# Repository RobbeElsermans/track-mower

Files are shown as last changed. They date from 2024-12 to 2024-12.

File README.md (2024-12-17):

# Track-Mower
A conceptual grass mower equipped with tracks for enhanced mobility.

## Overview
The Track-Mower is built around the ESP D1 Mini microcontroller, which provides WiFi, Bluetooth, and BLE capabilities. Communication between the driver and the mower is established via Bluetooth. Commands are sent as single characters, with each character corresponding to a specific action the mower will execute for a predefined duration.

## Features
- **Microcontroller**: ESP D1 Mini with WiFi, Bluetooth, and BLE.
- **Command-based Control**: Simple single-character commands for predefined actions.
- **Bluetooth Communication**: Reliable connection between the mower and a smartphone.

## How to Use
To operate the Track-Mower:
1. Install the [Serial Bluetooth Terminal](https://play.google.com/store/apps/details?id=de.kai_morich.serial_bluetooth_terminal) app on your Android device.
2. Pair your smartphone with the Track-Mower via Bluetooth.
3. Use the app to send commands to the mower.

## Command List
The following commands can be used to control the Track-Mower:

| Command | Action | Duration  | Description |
|---|---|---|---|
| **F** | Forward  | 1 second  | Moves the mower forward. |
| **B** | Backward | 1 second  | Moves the mower backward. |
| **R** | Right | 0.5 second| Turns the mower to the right using both tracks. |
| **L** | Left | 0.5 second| Turns the mower to the left using both tracks.  |
| **M** | Mower | Gradual | Spins up the blades gradually. |

### Example Usage
To drive the mower forward for 2 seconds, turn left, and then start the blades:
```
F
F
L
M
```

## What to print
- 1x [Battery_assemblyBattery_holder](track-mower/CAD/3D_printing/tank_mower-Battery_assemblyBattery_holder.stl)
- 1x [chassis_body_V2](track-mower/CAD/3D_printing/tank_mower-chassis_body_V2.stl )
- 2x [Track_assemblybearing002](track-mower/CAD/3D_printing/tank_mower-Track_assemblybearing002.stl )
- 2x [Track_assemblybearing_holder_out001](track-mower/CAD/3D_printing/tank_mower-Track_assemblybearing_holder_out001.stl )
- 4x [Track_assemblybearing_holder_out_608002](track-mower/CAD/3D_printing/tank_mower-Track_assemblybearing_holder_out_608002.stl )
- 6x [Track_assemblyExtender](track-mower/CAD/3D_printing/tank_mower-Track_assemblyExtender.stl )
- 2x [Track_assemblyFollower](track-mower/CAD/3D_printing/tank_mower-Track_assemblyFollower.stl )
- 6x [Track_assemblyOverWheel](track-mower/CAD/3D_printing/tank_mower-Track_assemblyOverWheel.stl )
- 2x [Track_assemblyPuller001](track-mower/CAD/3D_printing/tank_mower-Track_assemblyPuller001.stl )
- 58x [Track_assemblytrack](track-mower/CAD/3D_printing/tank_mower-Track_assemblytrack.stl )
- 2x [Track_assemblyTrack_plate](track-mower/CAD/3D_printing/tank_mower-Track_assemblyTrack_plate.stl )
- 6x [Track_assemblyWasher](track-mower/CAD/3D_printing/tank_mower-Track_assemblyWasher.stl)
- 1x [Track_assemblyWasher](track-mower/CAD/3D_printing/Blade.stl)

## Other things
- 608ZZ bearings
- M3 washers, nuts and bolts
- Hot glue
- PowerPlus adapter
- DC motors
- Controller board

## Future Improvements
Here are some ideas for future enhancements:
1. **Advanced Controller**: Develop a controller for precise real-time control of the Track-Mower.
2. **PCB Redesign**: Improve the PCB design to provide more stable current sensing.
3. **Code Optimization**: Refactor the codebase and port it to an RTOS for better performance and scalability.

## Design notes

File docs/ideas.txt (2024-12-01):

Design an electronic menu for ordering food in hospitals.
	--> The patient gets a custom menu for any history related subject.

Create a low-cost negative pressure system for removing fluid from wounds.
	--> Could be helping the wound healing process

Design a go---kart that can be controlled by a joystick for children paralyzed below the waist.
	--> They should also have some fun!

An alarm for an electrician to wear in case he ever got electrocuted
	--> This allerts first aid

Cheap Smart Wheelchair 
	--> Able to drive with joystick and smartphone
	--> Collects data (black box)

chrismas village lights 
	--> A living city

NO -> SMD reflow met strijkijzer met ESP32 en OLED.  

RGB controller, controllable over zigbee or WiFi and IR-led. Also measuring temp, hum & light and send it over on zigbee or WIFI.
	- MOSFET's for leds
	- Temperature sensor
	- Humidity Sensor
	- IR led receiver
	- RF-radio
	- Current sensor (statistical usage)
	- Power management
	- 3D printed case 
	- Lasercut? 

Create a low-cost negative pressure system for removing fluid from wounds.
	--> Could be helping the wound healing process
	- Air pump
	- Tubes 
	- valve?
	- pressure sensor
	- OLED for settings
	- buttons and/ or leds
	
Radio controlled tank mower (small one with "virtual" cutting knives)
	- H-bridge/ ESC
	- brushed / brushless motor
	- bearings
	- tank housing
	- tank tracks
	- gear reductions?
	- Power management
	- Battery powered
	- Controlling? PS3 controller (is bluetooth)

Walk logger for hiking

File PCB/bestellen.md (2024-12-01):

2x fuse holder https://mou.sr/489tumF
2x https://be.farnell.com/multicomp/mccq-121/fuseholder-pcb-mount-ato/dp/1586596

2x fuse 10A https://www.digikey.be/en/products/detail/littelfuse-inc/089107-5NXWS/5233824
https://be.farnell.com/littelfuse/166-7000-5102/automotive-fuse-10a-80vdc/dp/3515901

2x pot 1M https://www.digikey.be/en/products/detail/bourns-inc/TC33X-2-105E/2566882
https://be.farnell.com/bourns/tc33x-2-503e/trimmer-pot-50k-25-1turn-smd/dp/1689867

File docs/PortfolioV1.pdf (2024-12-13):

# Portfolio I-Prototyping

## Robbe Elsermans - s0220625

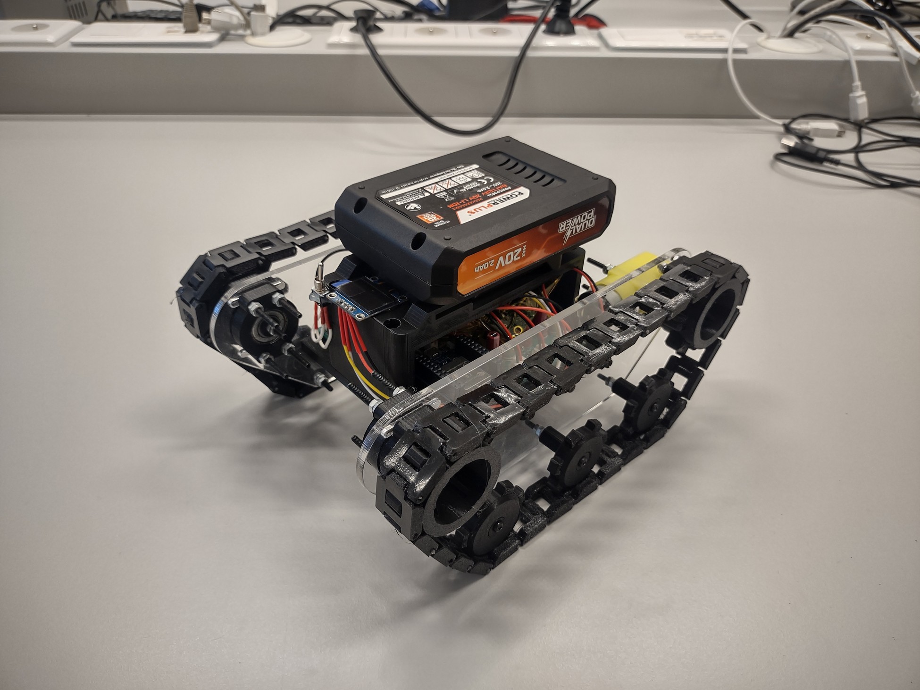
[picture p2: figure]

# Intro

In dit project voor het van I-Prototyping ga ik een rupsvoertuig grasmachine ontwerpen.

Waarom een rupsvoertuig grasmachine?

Een rupsvoertuig is zeer wendbaar in moeilijk bereikbare plaatsen. Echter moet hier soms ook

het gras/ struiken worden afgereden. Huidig doen ze dit met bulldozers waardoor de gehele

grond afgeschraapt wordt. Dit vernietigt het land waarbij bij het afmaaien, de grond intact blijft.

De manual van dit project staat beschreven in de README.md.

# Requirements

Om het project vlot te kunnen starten, heb ik allereerst een opsomming gemaakt wat het

rupsvoertuig grasmachine allemaal nodig kan hebben.

- Actuatoren
o | Motor track links
o | Motor track rechts
o | Motor maai blad
o | Led verlichting
- Sensoren
o | Stroom verbruik
o | Temperatuur
o | Snelheid
o | Locatie
o | Motor Encoder
- Mechanica
o | Rollagers
o | Chassis
o | Trekwielen
o | Volgwielen
o | Rupsband

# 3D model

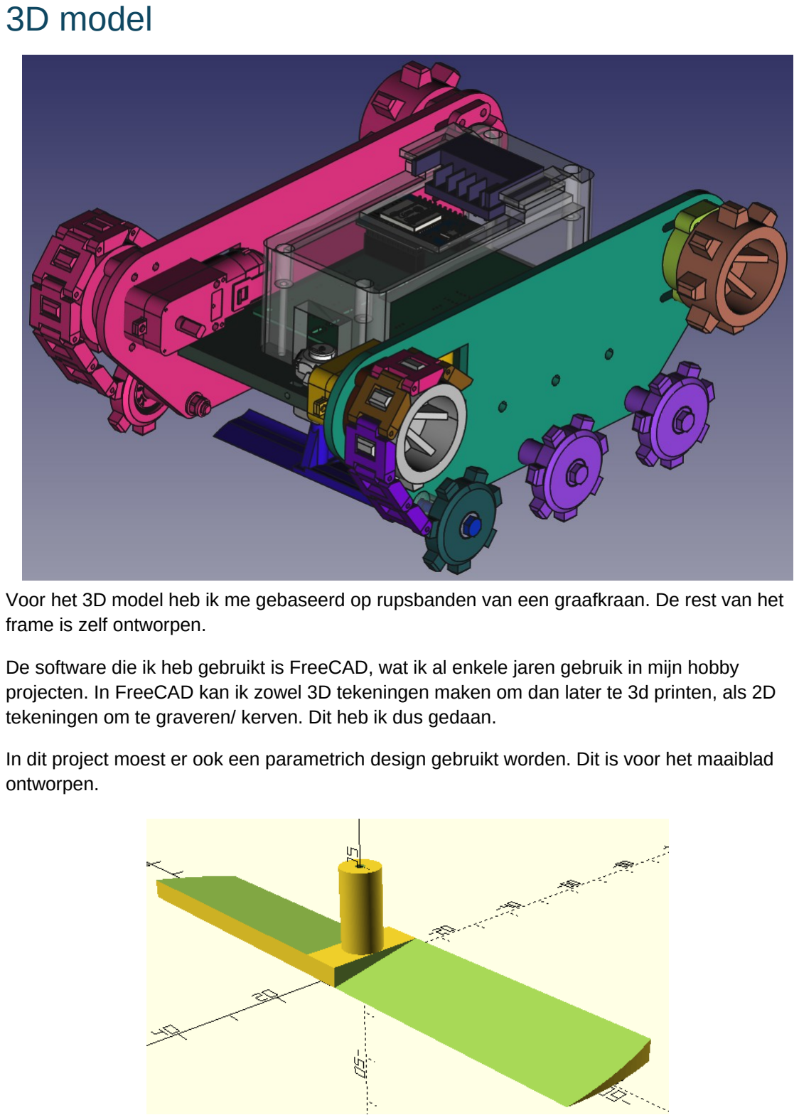
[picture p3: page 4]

Voor het 3D model heb ik me gebaseerd op rupsbanden van een graafkraan. De rest van het

frame is zelf ontworpen.

De software die ik heb gebruikt is FreeCAD, wat ik al enkele jaren gebruik in mijn hobby

projecten. In FreeCAD kan ik zowel 3D tekeningen maken om dan later te 3d printen, als 2D

tekeningen om te graveren/ kerven. Dit heb ik dus gedaan.

In dit project moest er ook een parametrich design gebruikt worden. Dit is voor het maaiblad

ontworpen.

De mechanische componenten zijn zo gekozen dat ze in elke ijzerwinkel te vinden zijn. Behalve

de motoren, deze zijn geselecteerd om op 5V te kunnen opereren en die niet te veel vermogen

vragen. Hierdoor kan ik componenten gebruiken die in het labo ter beschikking gesteld worden.

De rupsketting, zal een aaneenschakeling worden van deeltjes die de gehele rups maken. Om

de rupsketting op spanning te zetten, zal het achterste volgwiel, verschuifbaar zijn om zo de

rups aan te spannen.

De grondwielen zijn in dit design zonder enige vering. Dit zou het project complexer maken

waar jammer genoeg geen tijd voor is.

De plaat waarop de rups tracks geassembleerd word (links en rechts zijn spiegelbeeld), zal uit

Acryl 4mm bestaan die we d.m.v. de laserprinter gaan uitsnijden. Om deze 2 delen te

verbinden, maak ik gebruik van een 3d geprinte chassis. Hierop kan de elektronica en

batterij(en) gemonteerd worden, alsook de motor om het maai-blad aan te sturen.

Het maai-blad zal tussen de tracks staan, waardoor het gras onder het rupsvoertuig mooi kan

worden afgesneden zonder de rupsen of dergelijke te raken.

## 3D Print

De 3D geprinte onderdelen hebben allen een infill van 15%, 2 muren en 5 boven en onder

lagen met een afstand van 0.2mm. Alle onderdelen, behalve de rupsen, zijn in PLA geprint.

Voor de rupsen heb ik voor TPU gekozen omdat deze een elastische eigenschap heeft en ook

wat “plakkeriger” is aan ondergronden door deze elasticiteit. Door de elasticiteit, zal het

rupsvoertuig mobieler zijn op vlakke ondergronden.

De rupsen zijn aan elkaar geschakeld door kleine stukken filament van 1.75mm.

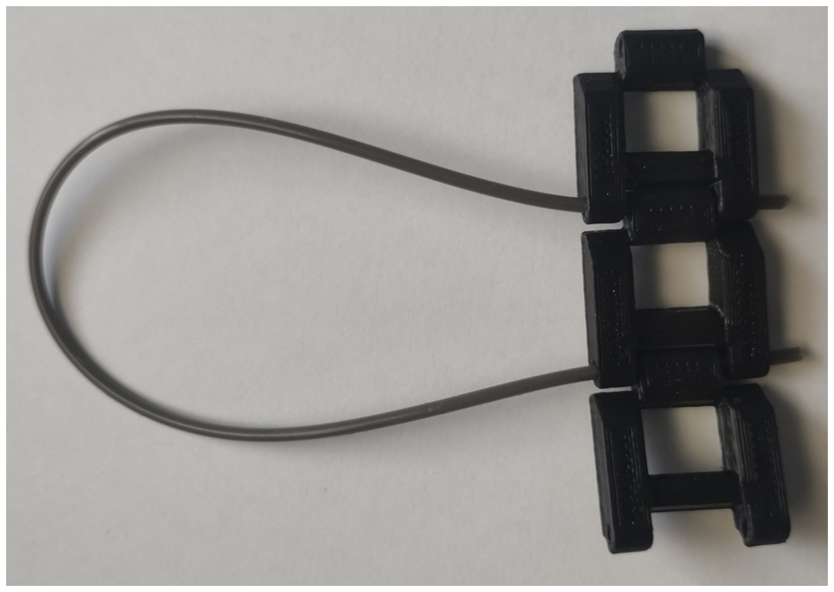
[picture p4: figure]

## Laser Cut

De laser cut machine is gebruikt om de track assemblage op te bevestigen. Deze is met een

snelheid van 15mm/min aan een power van 85% uitgesneden op een Acryl plaat van 4mm dik.

Er werd voor Acryl gekozen omdat deze tegen water kan. Als we gras versnijden, komt er water

vrij. MDF kan hier niet goed tegen.

# Blockschema

Om een globaal overzicht te bekomen, heb ik een blokschema gemaakt. Hierin duid ik aan

welke sensoren en actuatoren ik gebruik en de communicatie tussen deze componenten en de

microcontroller.

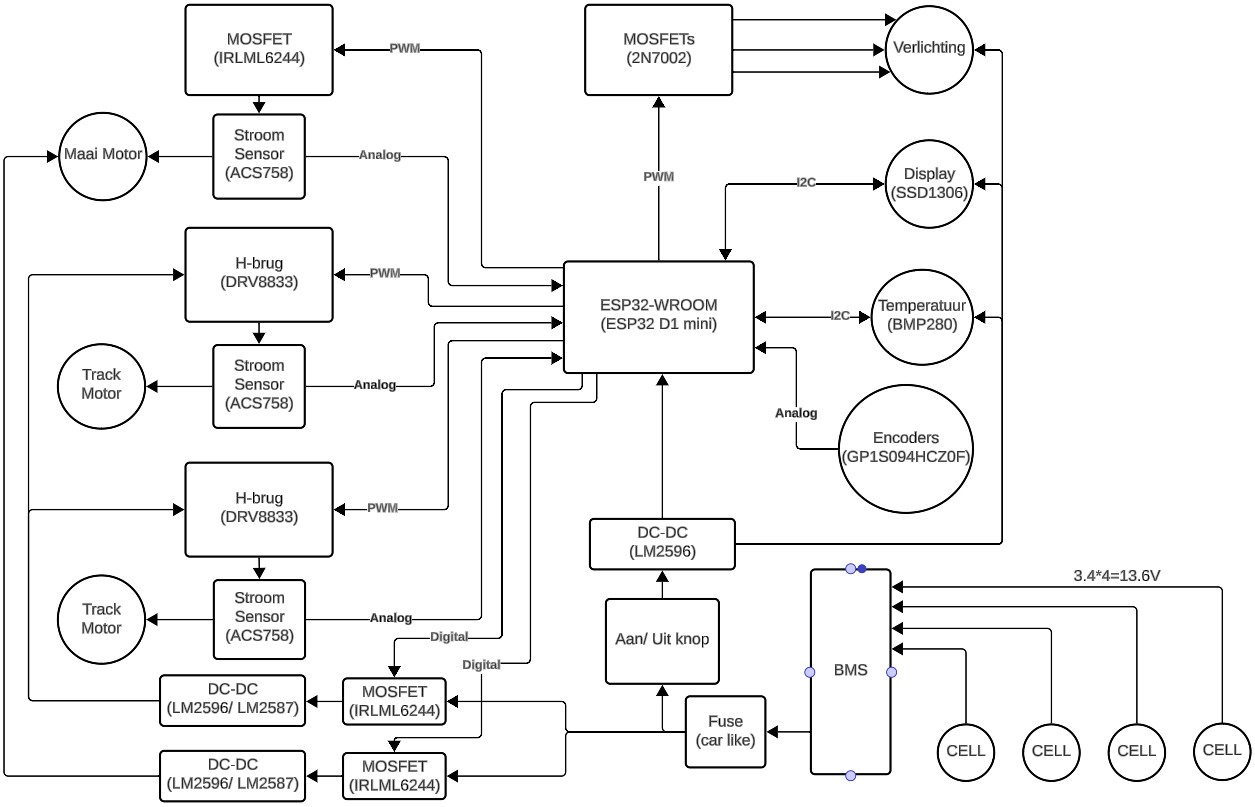
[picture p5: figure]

# Componenten

Referencie | Waarde | Aantal
C1,C4,C6,C7,C10,C24,C26,C28,C31,C32 | 10n | 10

# C2,C16,C17,C18,C19,C20,C21,C22,C23,C25,C27,C33,C34

,C39,C40,C41 | 10µ | 16
C3,C35,C36 | 1µ | 3
C5,C11 | 2.2µ | 2
C8,C14 | 100µ | 2
C9,C15 | 407µ | 2
C37 | 470µ | 1
D5 | D | 1
D6,D7,D8,D9 | LED | 4
D10 | D_Schottky | 1
F1 | MCCQ-121 | 1
J1,J2,J3 | LM2596_modul_in | 3
J4 | BMP280_Module | 1
J5 | BMS_input | 1
J6,J11,J12 | LM2596_modul_out | 3
J7 | On/Off_toggle | 1
J8 | SPI_Connector | 1
J9 | SSD1306 | 1
J10 | I2C_Extender | 1
J13,J14 | GP1S094HCZ0F | 2
M1,M2,M3 | Motor_DC | 3
Q3,Q10,Q12,Q13,Q14,Q15 | 2N7002 | 6
Q4,Q11,Q17 | SI2323 | 3
Q5 | IRLML6244 | 1
Q16,Q18 | Si7141DP | 2
R1,R2,R16,R22,R48,R49,R58,R60,R62 | 10k | 9
R3,R6,R7,R8,R9,R18,R19,R20,R21,R23,R25,R37,R38,R39,
R41,R42,R43,R44,R45,R46,R47,R55,R66 | 1M | 23
R4,R5,R30,R32,R34,R36 | 120 | 6
R10,R11,R12,R13,R14,R15,R40,R63 | 100k | 8
R17,R52,R53 | 3.3k | 3
R24,R50,R51 | 68k | 3
R26 | R | 1
R27,R28 | 4k7 | 2
R29,R31,R33,R35 | 10M | 4
R54 | 2.2M | 1
R56 | 3.3M | 1
R57,R59,R61 | 12k | 3
R64,R65 | 15k | 2

U1,U5,U11 | TLV2775AIN

3
U2,U6,U8 | ACS758xCB-050B-PFF

3
U4,U7 | DRV8833PWP

2
U9 | esp32-wemos-d1-mini

1
U10 | PCF8574

1

# Stroom Verbruik

Component | Maximaal Verbruik (A)
track motor (TT-Motor) | 1.5
track motor (TT-Motor) | 1.5
DC motor 6V | 0.5
Verlichting (LED) | 0.05
Verlichting (LED) | 0.05
Verlichting (LED) | 0.05
Verlichting (LED) | 0.05
Display (SSD1306) | 0.02
Encoder (GP1S094HCZ0F) | 0.05
Encoder (GP1S094HCZ0F ) | 0.05
H-brug (DRV8833) | 0
H-brug (DRV8833) | 0
Totaal | 3.83

De niet vermelde onderdelen hebben zeer kleine stromen die in deze configuratie geen impact

hebben.

# Berekeningen

## Battery voltage scaler

Om de batterij spanning te meten, moeten we gebruik maken van een spanningsdeler. We gebruiken namelijk een 5C Li-Ion (5 cell) batterij in serie geschakeld waardoor we een maximaal voltage krijgen van Vbat=5×4.2V=21V.

De ESP32 heeft een maximaal bereik tot Vcc=3.3V .

Om een zekere veiligheid marge te bekomen, gaan we er vanuit dat de maximale
batterijspanning Vbat=5×4.25V=21.25V is.

Er is dus een spanningsdeler nodig met factor

### Vin

### Vout

=

### V bat

### V cc

=

21.25V
3.3V

=6.43939 ...

De spanningsdeler formule is als volgt: Vout=Vin

R2
R2⁺R1

Stel, we nemen R2=1 M Ω, dan is R1=

VR2

### Vout

# − R2=6.43939∗1 M Ω−1M Ω=5.439 M

Nu voor de E-12 reeks, nemen we 3.3MΩ en 2.2MΩ om uit te komen op 5.5MΩ.

Deze verhoging in waarde, zal de spanning verlagen op de uitgang met een factor.
R2
R1⁺R2

=

1M Ω

# 5.5 MΩ+1MΩ

=0.15384

In code wordt de gemeten spanning dus vermenigvuldigt met | 1
0.153846154

=6.4999999=6.5

## Current sensor low-pass filter

De stroom sensor (met behulp van HALL-effect of elektromagnetisch veld) zal op een PWM gestuurde actuator aangesloten worden. De ingestuurde PWM wordt dus eveneens ingelezen door de sensor. Om de sensor uit te lezen, gaan we dus een analoge filter maken die ons signaal frequentie bereik beperkt van 0Hz tot 50Hz.

Hiermee merken we nog steeds verschillen op die tot en met 1
50Hz

=2ms veranderen.

We bepalen de nodige weerstand in de RC-filter.

f
c=

1

# 2 πRC

R=

1

### 2πf cC

met f

# c=50 Hzen C=1µF wordt dit R=

1

# 2 π50 Hz 1µF

=3183Ω

Of in E-12 reeks 3.3 k Ω. Wat een cut-off frequentie heeft van f
c=

1

# 2 π 3.3 kΩ1µF

=48.22Hz.

## Current sensor readout

De stroom sensor geeft een spanning die lineair verloopt met de gemeten stroom.

Bij 0A, is er een spanning van Viout=

### Vcc

2

waarbij Vcc=3.3V dus viout=1.65V .

Per ampère gemeten, komt hier 40mV bij. Dus algemeen 1.65V ± 40mV / A. Deze kan dus

zowel positief als negatieve stroom (inverse stroomzin) meten.

Doordat de ESP32, met zijn 12-bit ADC, een resolutie heeft van Δ=

3.3V

# 4096 bit =805. 664 µV

zou deze maar een stroom van Δ I=(
40 mV
A

805.664µV )

−1
=0.021416 A

per verschil in bit kunnen

meten. Dit is een te kleine resolutie.

We gaan dus de resolutie terugschroeven naar [−4 A , 4 A] wat het volgende geeft:

# Viout min=1.65V −4 A∗0.0 4

V
A

=1.49V

# Viout max=1.65V +4 A∗0.0 4

V
A

=1.81V

# V Δ=1.81V −1.49V =0.32V

Met een differentieel versterker, kunnen we de verschilspanning V Δ opmeten. We nemen een

versterking van 1. Nadien plaatsen we een niet-inverterende versterker met factor 10.

Deze brengt de spanning van maximaal 0.32V naar 3.2V.

Nu hebben we een een stroom van Δ I=(

400 mV
A

805.664µV )

−1
=0.0 021416 A

per verschil in bit dat

we kunnen meten.

Voor de differentieel versterker, nemen we vier dezelfde weerstanden van 100kΩ. Voor de

referentie spanning van 0 A of 1.49V, gebruiken we een spanning deler met hoge impedantie

ingang (een spanningsvolger). Deze zal met de weerstanden R1tot=1.215 M Ω en R2=1 M Ω.

Of beter een regelbare weerstand van 10kΩ gezet worden.

Voor de niet-inverterende versterker gebruiken we volgende formule om Rf te bepalen:

# Vout=V❑(1+

Rf

# R ) Met Vout=3.2V , V ❑=0.32V , R=10 k Ω geeft

Rf=(

### V out

V ❑

# −1)∗ R=9∗10 k Ω=90 k Ω

# Of in E-12 reeks 68kΩ+12kΩ+10kΩ

## Encoder comparator

De encoder zal een spanning geven in functie van de hoeveelheid licht op de LDR. Om het de MCU wat makkelijker te maken, gaan we dit signaal omzetten naar 2 waardes met een comparator. Dit om op de MCU een trigger te kunnen genereren wanneer er zo’n lichtbrug een object of geen object tussenin heeft.

De comparator zal bij een bepaald voltage, volledig Vcc of GND als uitgang geven.
De waardes die we gaan gebruiken zijn $V_low = 0.5V$ $V_high = 2.4V$. Dit omdat $V_BE =0.4V$.

V ❑=

# (V OH −Vref ) ∗R1

R1⁺R2

### +Vref

Waarbij we R_1 berekenen in excel. Wat het volgende geeft:

V_ref | v_TH | V_TL | R_1 | R_2 | R | V_N | V_P
1.65 | 0.825 | 2.475 | 10000 | 20000 | 2 | 0 | 3.3

Wat in simulatie het volgende geeft:

Met schaal 0.5V/div
Groen is out van opamp
Rood is in van opamp.

Dit is dus correct.

# PCB

Een 2-layer PCB waarbij tal van extra uitbreidingen en alternatieven zijn aangebracht.

Zo hebben we voor elke motor een stroom sensor. Met deze stroom sensor kunnen we bepalen

of dat een motor vast zit of niet. Om alias frequenties te vermijden, is een low-pass filter

toegevoegd. Ook het bereik van de stroom sensor is veel te groot voor de applicatie die weg

gaan gebruiken. Daarom gaan we een differentieel versterker nemen binnen een bepaald

bereik om de nauwkeurigheid te verbeteren binnen ons werkgebied. Zie berekeningen.

Er is een mogelijkheid om de motoren hun spanning omvormer af te zetten. Dit voor

bijvoorbeeld veiligheids-redenen. Er zou ook gewerkt kunnen worden met de LM2596 zijn

aan/uit pin (pin 5) om de spanning omvormer uit te schakelen. Echter is er gebruikt gemaakt

van opbouw modules waarbij deze pin niet naar buiten is gebracht.

De gebruikte motor sturing component (DRV8833) is een chip dat 2 H-bruggen bezit. De

DRV8833 kan een maximaal stroom verwerken van 1.5A (PWP package) per brug. Deze

bruggen kunnen we in parallel aaneen schakelen om dan dubbel zo veel vermogen uit te

brengen. Dus 3A per chip.

De gebruikte motoren geven bij een hoge belasting, 1.5A. We kunnen dus 1 chip per motor

gebruiken (de 2 h-bruggen parallel).

Voor de maai motor, is er gebruikt gemaakt van een N-MOSFET die maar in 1 richting kan

geleiden. De maai motor moet ook maar in 1 richting draaien.

De track motoren zijn brushed motoren die we niet d.m.v. de aansturing kunnen opvolgen i.v.m.

De snelheid. Dit zal dus met een extra component gebeuren genaamd een encoder. Voor de

encoder, maken we gebruik van een lichtbrug en een extra encorder-ring op de motor

geassembleerd. De gebruikte lichtbrug (GP1S094HCZ0F) is een analoog signaal dat lineair

verloopt met de lichtintensiteit. Om dit makkelijk te interpreteren in de MCU, gaan we een

comparator gebruiken om het analoog signaal, als een digitaal signaal aan te leggen bij een

bepaalde treshold (zie berekeningen).

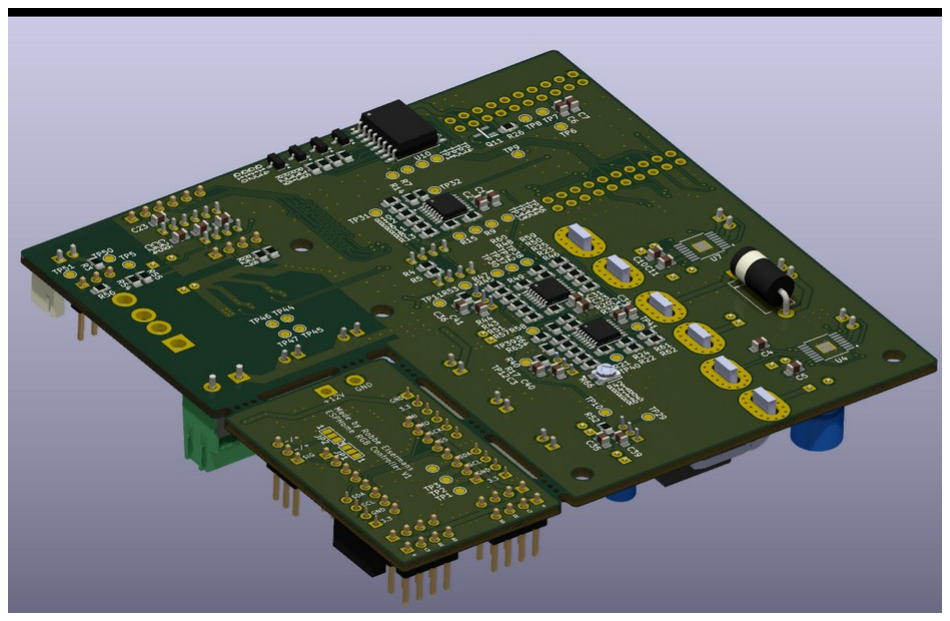
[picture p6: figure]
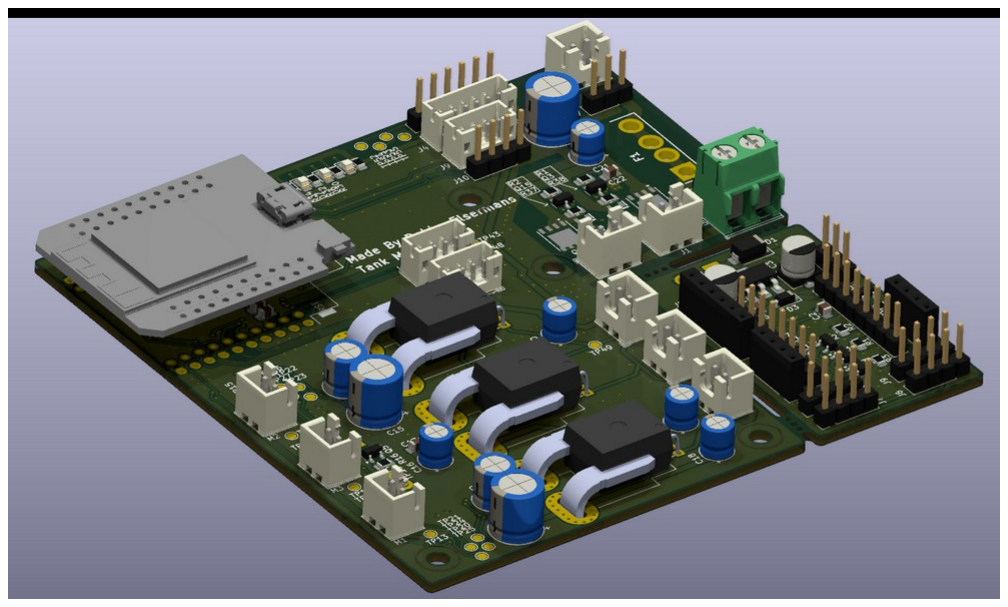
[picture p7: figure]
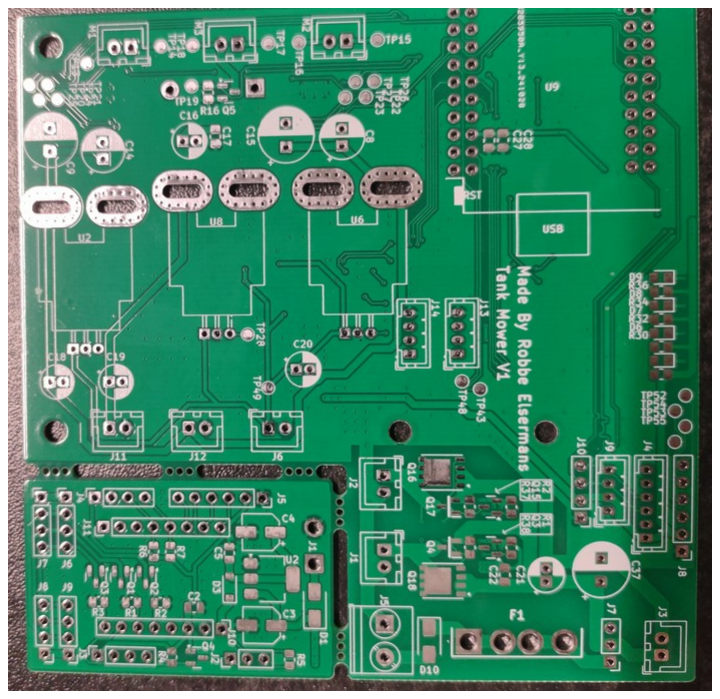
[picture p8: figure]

# Assemblage en testing

Bij het source van de nodige componenten heb ik opgemerkt dat ik een verkeerde package heb

genomen voor de quad-opamp module (TLV2775) namelijk TSSOP. Echter heeft deze een

package van SOP wat dus een verschil geeft. Jammer genoeg was de pcb al in productie

gezet. Dus er was nood aan een nieuwe component met dezelfde footprint en package.

Na wat zoeken is er het volgende gevonden: TLV4333IPWR. Er is een groot verschil in GBP,

maar de toepassing waarin ik deze opamps gebruik mag de GBP laag zijn. Het zijn tenslotten

laag frequente signalen.

Bij het solderen ben ik gestart met al de SMD componenten te solderen beginnende bij de

laagste packages. Voor het solderen, werd er gebruik gemaakt van een SMD reflow plate die

zelf is ontworpen.

Om de PCB grondig te testen, zal ik deze deel per deel opbouwen om zo de werking ervan te

testen.

## I2C bus

Nadien de ESP32, IO-expansie module alsook de 4 leds om te valideren dat de IO-expansie

module correct kan gebruikt worden. Ook de OLED module werd aangesloten.

Om de test visueel te valideren, wordt er 1010 op de OLEd getoond en ook de leds kleuren in

een 1010 patroon.

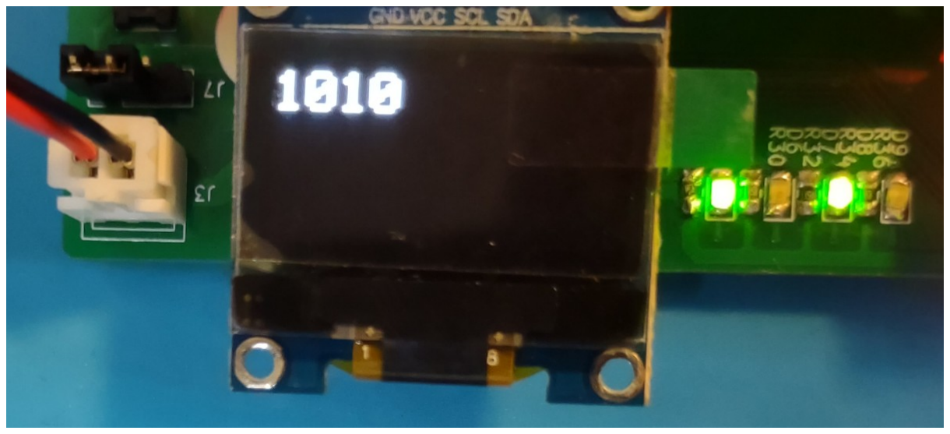
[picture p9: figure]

## VCC switch

Daarna werd de motor P-MOSFETS bevestigd. Na het correct afstellen van de buck-converters

hun uitgangsspanningen, zijn deze door verbonden met de PCB.

Bij het testen van de schakelaars, was er één pin die niet aan of uit wou gaan. Na verder

onderzoek blijkt deze pin (35) een input only pin te zijn. Echter gebruik ik deze als output. Om

dit op te lossen, zal de andere pin (13) gebruikt worden om beide te schakelen. Dit kon

makkelijk opgelost worden door een connectie te maken tussen de testpunten TP43 en TP48.

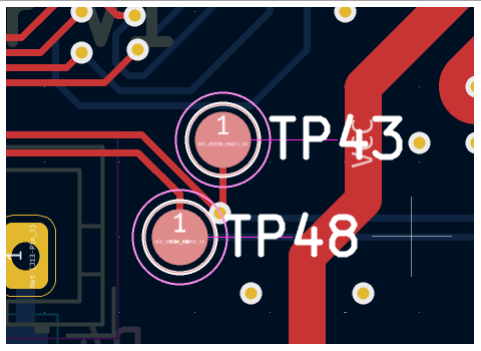
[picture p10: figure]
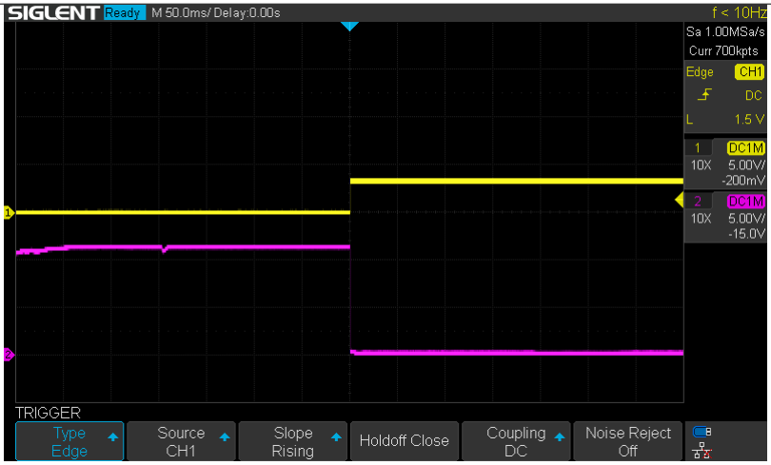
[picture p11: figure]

Scoope beeld waarbij te zien is dat pin 13 hoog komt (GEEL), en daardoor zal ook Q15 en

Q17 schakelen als ook Q16 en Q18 waardoor de Buck-modules gevoed worden met de input

spanning. Aan de gates (PAARS) van de P-MOSFET zal de pull-up spanning dus dalen naar

0V en zo zal de P-MOSFET in geleiding treden.

## H-Brug

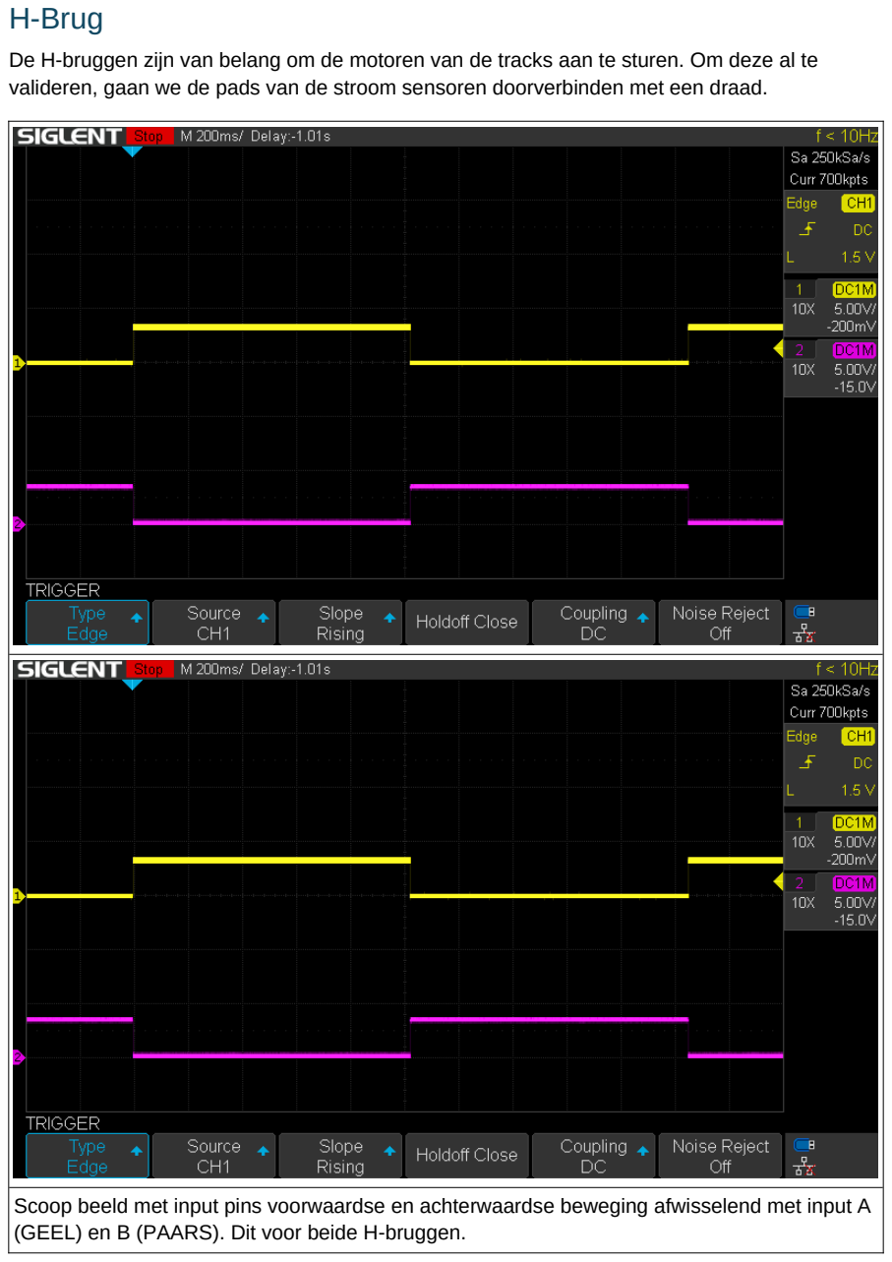
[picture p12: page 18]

De H-bruggen zijn van belang om de motoren van de tracks aan te sturen. Om deze al te

valideren, gaan we de pads van de stroom sensoren doorverbinden met een draad.

Scoop beeld met input pins voorwaardse en achterwaardse beweging afwisselend met input A

(GEEL) en B (PAARS). Dit voor beide H-bruggen.

## Current sensor

Vervolgens werden de stroom sensoren bevestigd. De stroom sensoren zijn van belang om te

bepalen wanneer een motor niet meer kan bewegen door een obstakel of dergelijke. Daarom

zijn er stroom sensoren voorzien die elke motor hun stroom kan meten met een nauwkeurigheid van 2mA en een bereik van [−4 A, 4 A].

FOTO

testopstelling 330Ω weerstand als verbruiker wat 0.05050A neemt bij 5V op de mower motor

connector. Deze is geselecteerd om het makkelijk te kunnen schakelen door de N-MOSFET.

I=

10V
330Ω

=0.05050 A

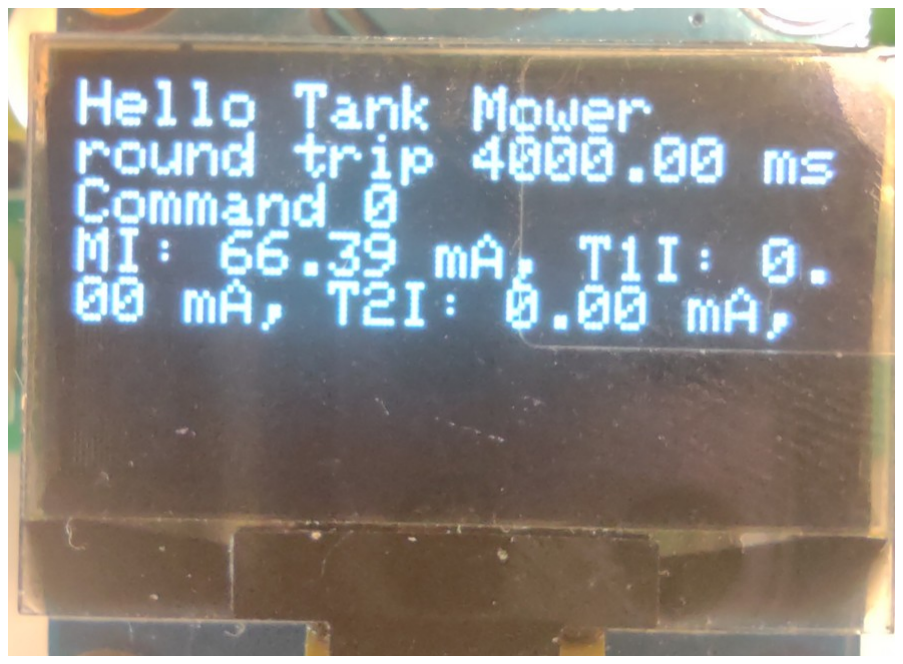
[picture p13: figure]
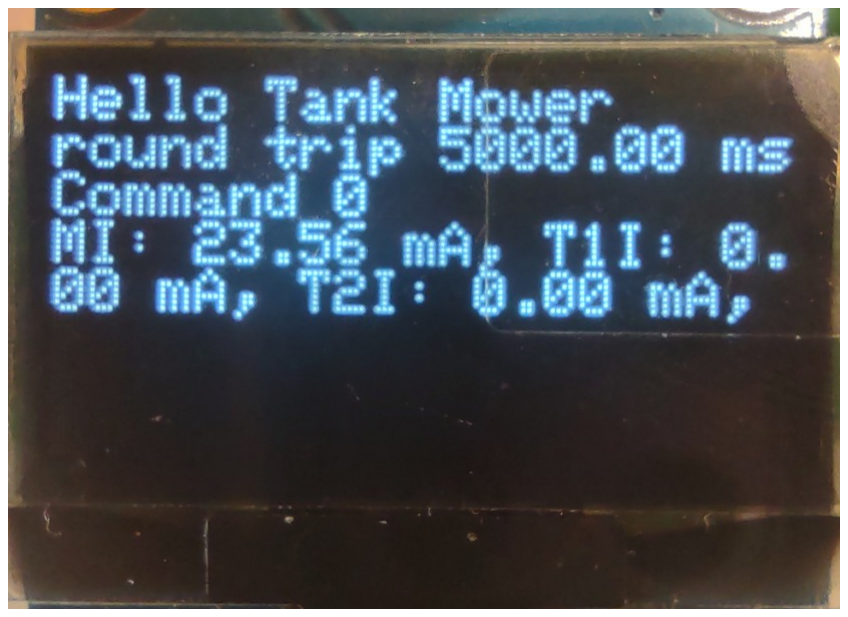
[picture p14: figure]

Op de metingen is duidelijk te zien dat er vrij veel fluctuaties op zitten. Dit komt

hoogswaarschijnlijk door de weerstand tolleranties die een orde groote hebben van 10%. Dit

kan dus de differentiaal versterker en de niet-inverterende versterker van factor 10 beinvloeden

## LP-filter

Om de werking van de LP-filter te valideren, werd er een sinus injectie uitgevoerd op de uitgang

van de stroom sensor die de stroom meet op de mower-motor. De gebruikte sinus is 25Hz,

250Hz en 2.5kHz.

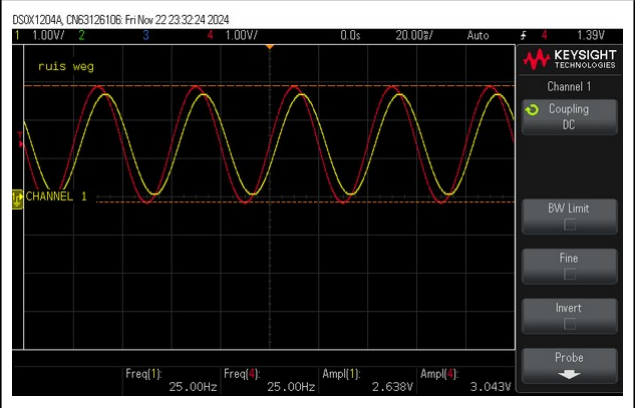
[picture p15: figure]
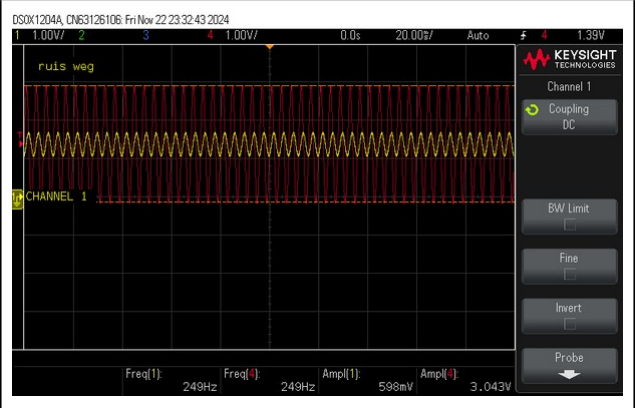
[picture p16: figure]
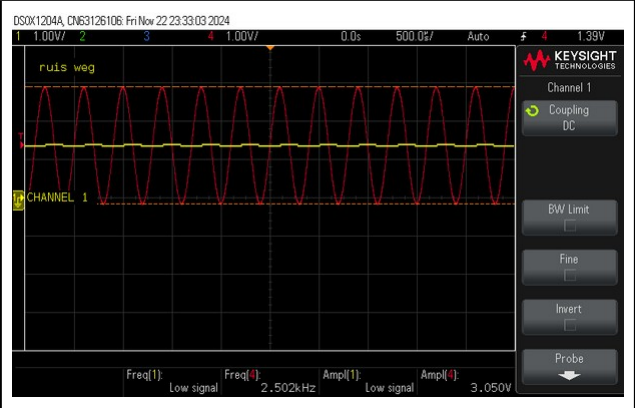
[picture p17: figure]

Scoop beeld met de sinus functie injectie (ROOD) en de response van de LP-filter (GEEL).

25Hz, 250Hz en 2k5Hz respectievelijk.

Er is een mooie attenuatie te zien.

## Batterij spanning

De batterij spanning wordt d.m.v. een spanningsdeler ingelezen in de ESP. Hier maken we

gebruik van een factor 6.5 om de effectieve spanning te weten. We leggen een spanning aan

van 12V wat zou moeten uitkomen op 1.847V.

Echter is hier een probleem met de gekozen pin 12. Wanneer pin 12 niet floating is bij boot, zal

de boot falen. Dit mond uit dat de ESP niet kan opstarten als er een batterij is aangesloten.

Om dit toch te kunnen gebruiken, zijn de functies van pin 12 en pin 35 omgedraait. Hierdoor zijn

beide functies beschikbaar.

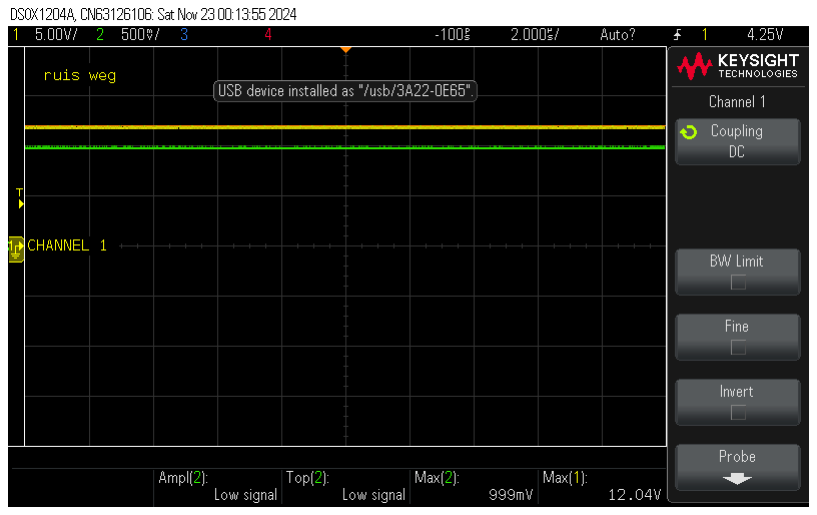
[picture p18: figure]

Een scoop beeld waarbij de ingangsspanning (GEEL) is vergeleken met de uitgangsspanning

na de spanningsdeler (GROEN).

De vooropgestelde waarde van 1.847V blijkt niet te kloppen. Daarom gaan we in de code de

vermenigvuldiger factor wijzigen van 6.5 naar 12.

# Software

Om de complexiteit niet te verhogen, heb ik geen gebruik gemaakt van FreeRTOS om de tank

aan te sturen. De code bevat een finite-state machine waarbij alles zonder enige blocking calls

verloopt (een continue loop).

Hieronder een klein blok diagram die high level uitbeeld wat de code doet.

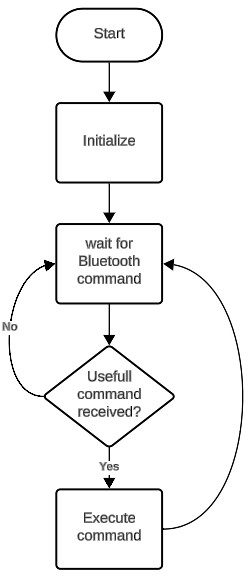
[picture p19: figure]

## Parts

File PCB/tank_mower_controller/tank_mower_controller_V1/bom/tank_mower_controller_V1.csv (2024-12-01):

Reference | Value | Datasheet | Footprint | Qty | DNP
C1,C4,C6,C7,C10,C24,C26,C28,C31,C32 | 10n | ~ | Capacitor_SMD:C_0805_2012Metric_Pad1.18x1.45mm_HandSolder | 10
C2,C16,C17,C18,C19,C20,C21,C22,C23,C25,C27,C33,C34,C39,C40,C41 | 10µ | ~ | -- mixed values -- | 16
C3,C35,C36 | 1µ | ~ | -- mixed values -- | 3
C5,C11 | 2.2µ | ~ | Capacitor_SMD:C_0805_2012Metric_Pad1.18x1.45mm_HandSolder | 2
C8,C14 | 100µ | ~ | Capacitor_THT:CP_Radial_D6.3mm_P2.50mm | 2
C9,C15 | 407µ | ~ | Capacitor_THT:CP_Radial_D8.0mm_P3.50mm | 2
C37 | 470µ | ~ | Capacitor_THT:CP_Radial_D8.0mm_P3.50mm | 1
D5 | D | ~ | Diode_THT:D_DO-201_P12.70mm_Horizontal | 1
D6,D7,D8,D9 | LED | ~ | LED_SMD:LED_0805_2012Metric_Pad1.15x1.40mm_HandSolder | 4
D10 | D_Schottky | ~ | Diode_SMD:D_SMA | 1
F1 | MCCQ-121 |  | mccq-121:MCCQ121 | 1
J1,J2,J3 | LM2596_modul_in | ~ | Connector_JST:JST_XH_B2B-XH-A_1x02_P2.50mm_Vertical | 3
J4 | BMP280_Module | ~ | Connector_JST:JST_PH_B6B-PH-K_1x06_P2.00mm_Vertical | 1
J5 | BMS_input | ~ | TerminalBlock_Phoenix:TerminalBlock_Phoenix_PT-1,5-2-5.0-H_1x02_P5.00mm_Horizontal | 1
J6,J11,J12 | LM2596_modul_out | ~ | Connector_JST:JST_XH_B2B-XH-A_1x02_P2.50mm_Vertical | 3
J7 | On/Off_toggle | ~ | Connector_PinHeader_2.54mm:PinHeader_1x03_P2.54mm_Vertical | 1
J8 | SPI_Connector | ~ | Connector_PinHeader_2.54mm:PinHeader_1x06_P2.54mm_Vertical | 1
J9 | SSD1306 | ~ | Connector_JST:JST_PH_B4B-PH-K_1x04_P2.00mm_Vertical | 1
J10 | I2C_Extender | ~ | Connector_PinHeader_2.54mm:PinHeader_1x04_P2.54mm_Vertical | 1
J13,J14 | GP1S094HCZ0F | ~ | Connector_JST:JST_PH_B4B-PH-K_1x04_P2.00mm_Vertical | 2
M1,M2,M3 | Motor_DC | ~ | Connector_JST:JST_XH_B2B-XH-A_1x02_P2.50mm_Vertical | 3
Q3,Q10,Q12,Q13,Q14,Q15 | 2N7002 | https://www.onsemi.com/pub/Collateral/NDS7002A-D.PDF | Package_TO_SOT_SMD:SOT-23 | 6
Q4,Q11,Q17 | SI2323 | ~ | SI-2323:SOT95P237X112-3N | 3
Q5 | IRLML6244 | https://www.infineon.com/dgdl/Infineon-IRLML6244-DataSheet-v01_01-EN.pdf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 | Package_TO_SOT_SMD:SOT-23 | 1
Q16,Q18 | Si7141DP | https://www.vishay.com/docs/65596/si7141dp.pdf | Package_SO:PowerPAK_SO-8_Single | 2
R1,R2,R16,R22,R48,R49,R58,R60,R62 | 10k | ~ | Resistor_SMD:R_0805_2012Metric_Pad1.20x1.40mm_HandSolder | 9
R3,R6,R7,R8,R9,R18,R19,R20,R21,R23,R25,R37,R38,R39,R41,R42,R43,R44,R45,R46,R47,R55,R66 | 1M | -- mixed values -- | -- mixed values -- | 23
R4,R5,R30,R32,R34,R36 | 120 | ~ | Resistor_SMD:R_0805_2012Metric_Pad1.20x1.40mm_HandSolder | 6
R10,R11,R12,R13,R14,R15,R40,R63 | 100k | ~ | Resistor_SMD:R_0805_2012Metric_Pad1.20x1.40mm_HandSolder | 8
R17,R52,R53 | 3.3k | ~ | Resistor_SMD:R_0805_2012Metric_Pad1.20x1.40mm_HandSolder | 3
R24,R50,R51 | 68k | ~ | Resistor_SMD:R_0805_2012Metric_Pad1.20x1.40mm_HandSolder | 3
R26 | R | ~ | Resistor_SMD:R_0805_2012Metric_Pad1.20x1.40mm_HandSolder | 1
R27,R28 | 4k7 | ~ | Resistor_SMD:R_0805_2012Metric_Pad1.20x1.40mm_HandSolder | 2
R29,R31,R33,R35 | 10M | ~ | Resistor_SMD:R_0805_2012Metric_Pad1.20x1.40mm_HandSolder | 4
R54 | 2.2M | ~ | Resistor_SMD:R_0805_2012Metric_Pad1.20x1.40mm_HandSolder | 1
R56 | 3.3M | ~ | Resistor_SMD:R_0805_2012Metric_Pad1.20x1.40mm_HandSolder | 1
R57,R59,R61 | 12k | ~ | Resistor_SMD:R_0805_2012Metric_Pad1.20x1.40mm_HandSolder | 3
R64,R65 | 15k | ~ | Resistor_SMD:R_0805_2012Metric_Pad1.20x1.40mm_HandSolder | 2
TP1,TP2,TP3,TP4,TP5,TP6,TP7,TP8,TP9,TP10,TP11,TP12,TP13,TP14,TP15,TP16,TP17,TP18,TP19,TP20,TP21,TP22,TP23,TP24,TP25,TP26,TP27,TP28,TP29,TP30,TP31,TP32,TP33,TP34,TP35,TP36,TP37,TP38,TP39,TP40,TP41,TP42,TP43,TP44,TP45,TP46,TP47,TP48,TP49,TP50,TP51,TP52,TP53,TP54,TP55 | TestPoint | ~ | TestPoint:TestPoint_Pad_D1.5mm | 55
U1,U5,U11 | TLV2775AIN | TLV2775AIN | Package_SO:TSSOP-16_4.4x5mm_P0.65mm | 3
U2,U6,U8 | ACS758xCB-050B-PFF | http://www.allegromicro.com/~/media/Files/Datasheets/ACS758-Datasheet.ashx?la=en | Sensor_Current:Allegro_CB_PFF | 3
U4,U7 | DRV8833PWP | http://www.ti.com/lit/ds/symlink/drv8833.pdf | Package_SO:HTSSOP-16-1EP_4.4x5mm_P0.65mm_EP3.4x5mm_Mask2.46x2.31mm_ThermalVias | 2
U9 | esp32-wemos-d1-mini |  | ESP32 D1 Mini:esp32-wemos-d1-mini | 1
U10 | PCF8574 | http://www.nxp.com/docs/en/data-sheet/PCF8574_PCF8574A.pdf | Package_SO:SOIC-16W_7.5x10.3mm_P1.27mm | 1

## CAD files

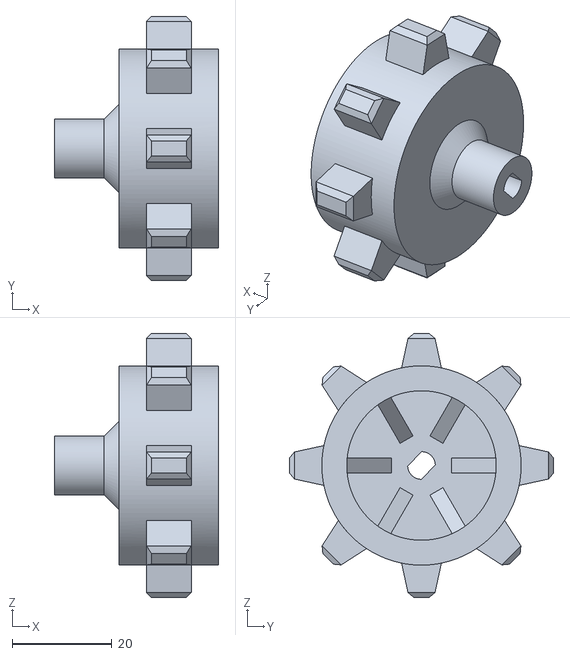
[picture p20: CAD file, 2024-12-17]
CAD/3D_printing/tank_mower-Track_assemblyPuller001.stl
33.0 x 53.0 x 53.0

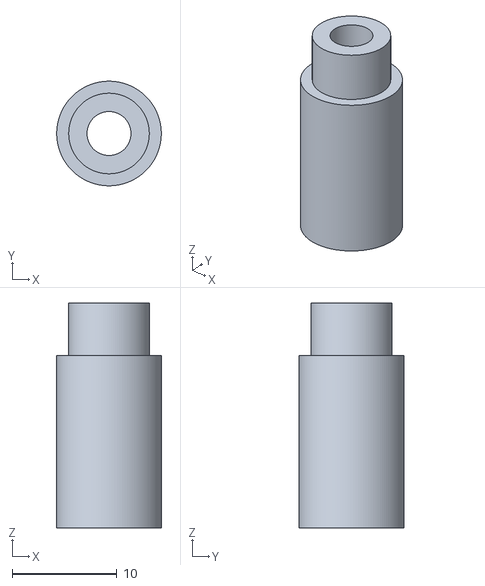
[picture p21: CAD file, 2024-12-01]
CAD/To_3D_print/tank_mower-Track_assemblyExtender.stl
10.00 x 10.0 x 21.5

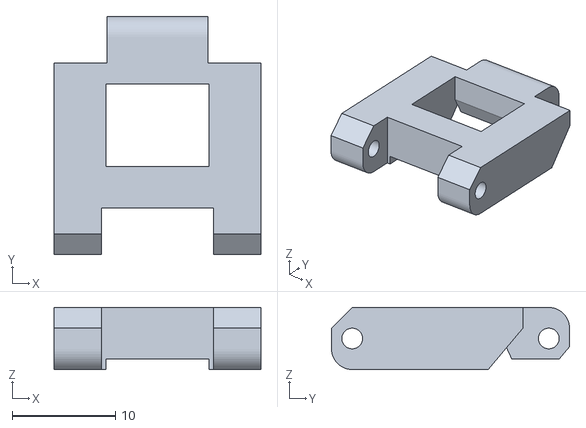
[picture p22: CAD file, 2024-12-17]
CAD/3D_printing/tank_mower-Track_assemblytrack.stl
20.0 x 23.0 x 6.00

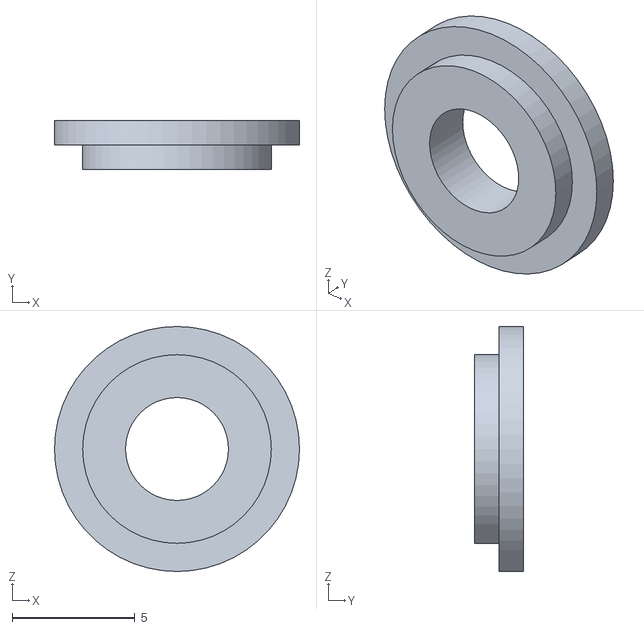
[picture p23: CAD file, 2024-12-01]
CAD/tank_mower-Track_assemblyPocket008.stl
10.0 x 2.00 x 10.0

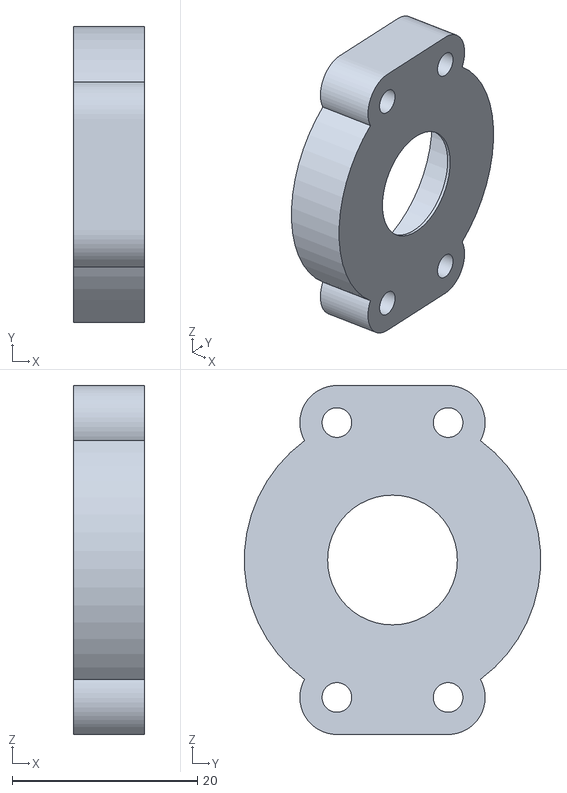
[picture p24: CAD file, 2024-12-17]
CAD/3D_printing/tank_mower-Track_assemblybearing_holder_out001.stl
7.70 x 31.9 x 37.7

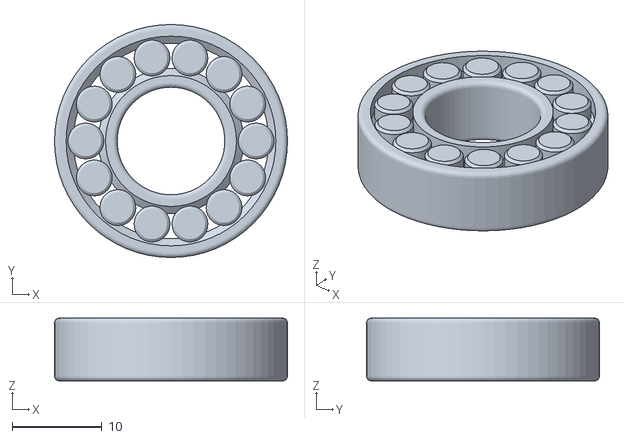
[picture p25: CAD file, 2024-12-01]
CAD/To_3D_print/tank_mower-Track_assemblybearing002.stl
26.0 x 26.0 x 7.00

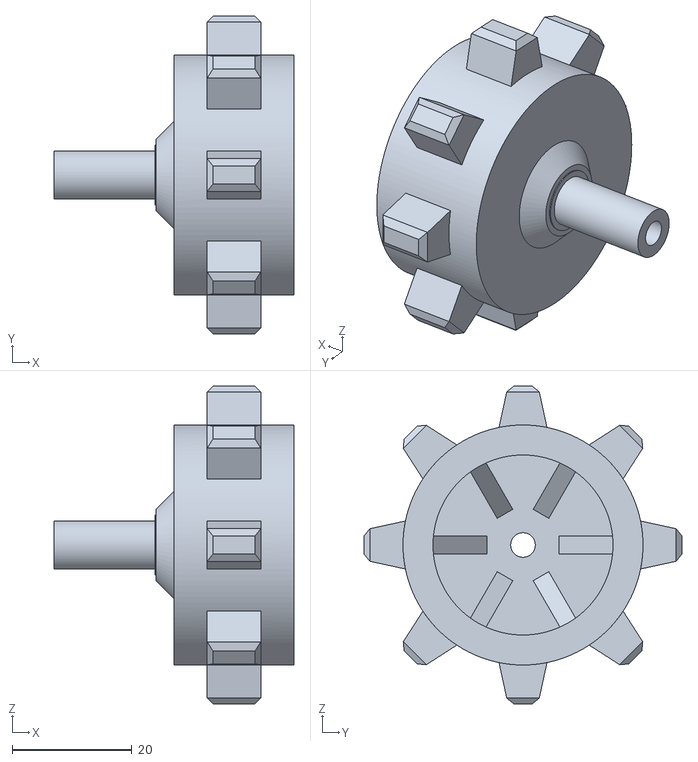
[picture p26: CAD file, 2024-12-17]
CAD/3D_printing/tank_mower-Track_assemblyFollower.stl
40.0 x 53.0 x 53.0

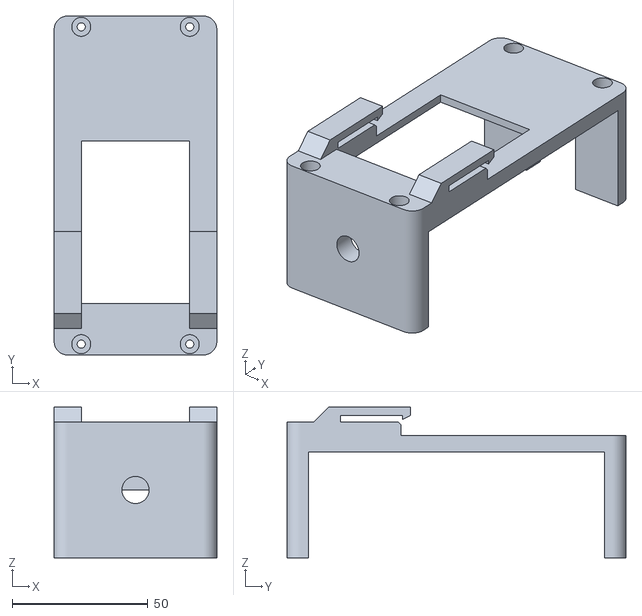
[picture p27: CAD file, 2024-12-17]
CAD/3D_printing/tank_mower-Battery_assemblyBattery_holder.stl
60.0 x 125.0 x 55.5

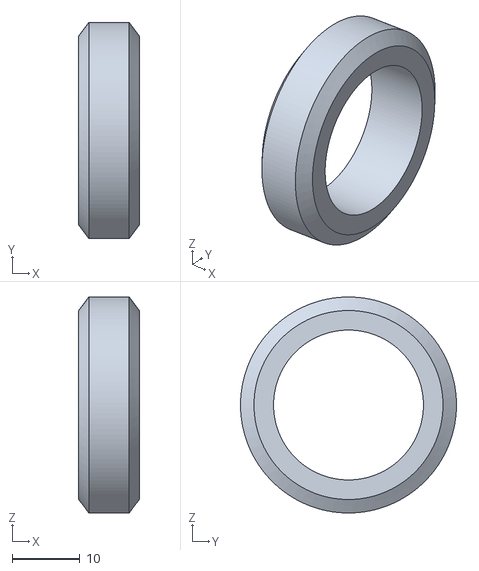
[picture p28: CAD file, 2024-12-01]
CAD/tank_mower-Track_assemblyroller.stl
9.00 x 32.0 x 32.0

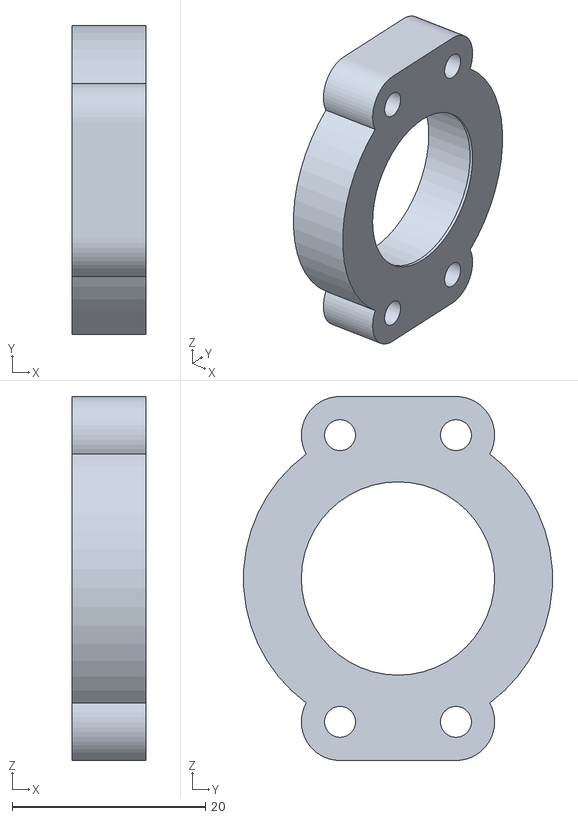
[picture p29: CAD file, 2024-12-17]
CAD/3D_printing/tank_mower-Track_assemblybearing_holder_out_608002.stl
7.70 x 31.9 x 37.7

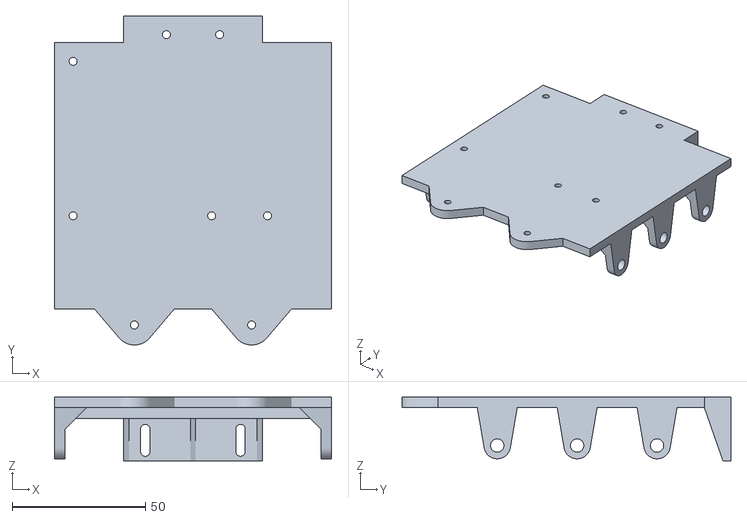
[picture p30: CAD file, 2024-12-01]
CAD/tank_mower-Chassy_body.stl
104.0 x 123.5 x 24.0

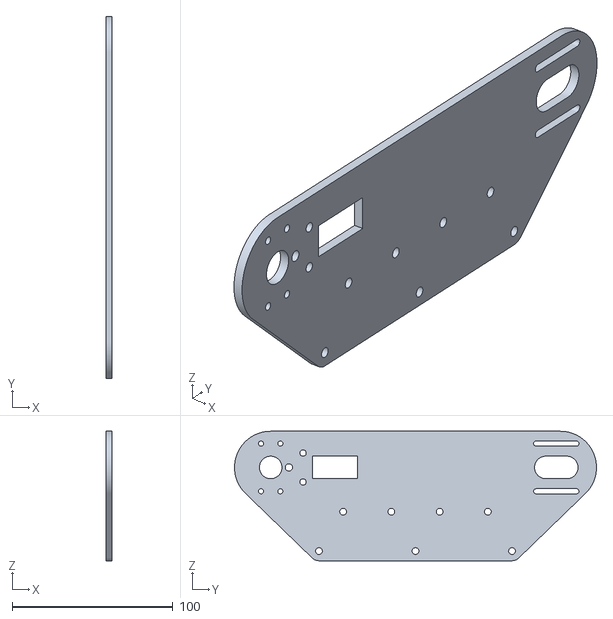
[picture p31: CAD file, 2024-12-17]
CAD/3D_printing/tank_mower-Track_assemblyTrack_plate.stl
4.00 x 225.0 x 80.5

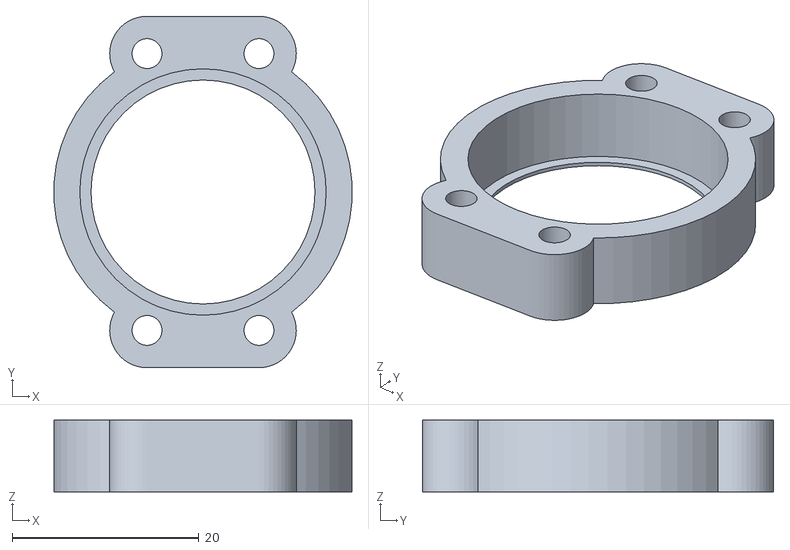
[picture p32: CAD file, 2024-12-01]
CAD/To_3D_print/tank_mower-Track_assemblybearing_holder_out001.stl
31.9 x 37.7 x 7.70

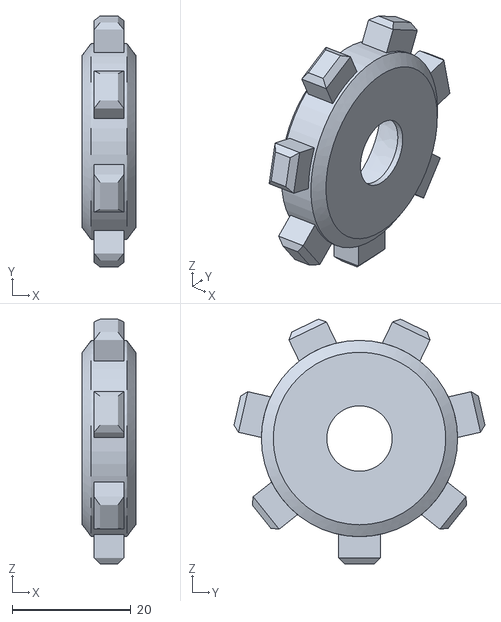
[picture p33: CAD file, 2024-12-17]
CAD/3D_printing/tank_mower-Track_assemblyOverWheel.stl
9.00 x 42.2 x 41.1

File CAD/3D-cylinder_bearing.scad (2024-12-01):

/* [Preview] */
// Enable preview of the crosssection.
print_view = 1; // [0:Cutted_view, 1:Print_view]

/*[Ball Bearing Dimensions]*/
// Height of the bearing.
height = 7.0;
// Inner ring radius. Half of the diameter.
inner_radius = 12/2; //[2:0.5:50]
// Inner ring radius. Half of the diameter.
outer_radius = 26.0/2; //[5:0.5:100]
// Radii of the inner and outer ring touching the housing and axis.
edge_radius = 0.5; //[0.0:0.1:2.0]
// Dimension of the rolling element.
ball_radius = 2; //[1:0.5:10]
// Edge Radii of the rolling element.
ball_edge_radius = 0.3; //[0.0:0.1:2.0]

/* [Spacing] */

/* [Spacing] */

/* [Spacing] */
// Space between the rolling element and each rin10g.
space_ball_rings = 0.2; //[0.0:0.05:0.5]
// Minimum space between the rolling elements. Effects the number of rolling elements.
min_space_between_balls = 0.25; //[0.0:0.05:1.0]
// Clearance between height of the rings and the height rolling elements. 
ball_height_space = 0.0; //[0.0:0.2:2.0]

/* [Guidance] */
// Ratio of height of the guidance elevation.
guide_size_ratio = 0.5; //[0.1:0.05:1.0]
// Elevation of the guidance element.
ball_guide_height = 0.8; //[0.1:0.1:10]

/*[Calculated Variables]*/
radi_diff = outer_radius - inner_radius;
ball_pos_radius = radi_diff/2 + inner_radius;
length_ball_pos_line = 2 * PI * ball_pos_radius;
num_balls = floor(length_ball_pos_line/(ball_radius*2+min_space_between_balls));
ball_angle_step = 360/num_balls;
guide_height = height * guide_size_ratio/2;

if (print_view==1) {
    bearing();
} else {
    difference() {
        bearing();
        translate([outer_radius/2, -outer_radius/2, height/2])
        cube([outer_radius,outer_radius, height+1], center=true);
    }
}


module bearing() {

    translate([0,0,height/2])
    union() {
        rotate_extrude($fn = 64) {
            translate([ball_pos_radius,0,0])
            union() {
                difference(){     
                    minkowski(){
                        square([radi_diff-2*edge_radius,height-2*edge_radius], center=true);
                        circle(r = edge_radius, $fn=16);
                    }
                    square([(ball_radius+space_ball_rings)*2, height + 1], center=true);
                }
                difference() {
                    for (angle = [0:180:180]) {
                        rotate([0,0,angle])    
                        translate([(ball_radius+space_ball_rings),0,0]) 
                        difference() {
                            rotate([0,0,45]) 
                            square(guide_height*sqrt(2), center=true);
                            translate([guide_height,0,0])
                            square(guide_height*2,center=true);
                        }
                    } 
                    square([(ball_radius+space_ball_rings-ball_guide_height)*2, height + 1], center=true);
                }
            }
        }
        
        for (angle_ball = [0 : ball_angle_step : 360]) {
            rotate([0,0,angle_ball])
            translate([ball_pos_radius,0,0])
            rotate_extrude($fn = 32) {
                union() {
                    translate([(ball_radius/2),0,0])
                    difference() {    
                        minkowski(){
                            square([(ball_radius-2*ball_edge_radius), height-2*ball_height_space-2*ball_edge_radius], center=true);
                            circle(r = ball_edge_radius, $fn=4);
                        }
                        translate([(ball_radius/2),0,0])
                        rotate([0,0,45])
                        square(guide_height*sqrt(2), center=true);
                    }
                    translate([((ball_radius-ball_guide_height)/2),0,0])
                    square([(ball_radius-ball_guide_height), height-ball_height_space*2], center=true);
                }
            }
        }
    }
}

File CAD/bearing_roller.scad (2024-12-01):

//Bearing 608 dimmentions
608_in_d = 8; //8mm hole diameter
608_out_d = 22;
608_width = 7;

tollerance = 0.0;

//Following wheel dimentions
follow_wheel_out_d = 608_out_d + (3 * 2); //3mm on each side
follow_wheel_in_d = 608_out_d + tollerance;
follow_wheel_cover_cap_depth = 1;
follow_wheel_depth = 608_width + follow_wheel_cover_cap_depth;

$fn=100;

linear_extrude(follow_wheel_depth)
difference()
{
    circle(d = follow_wheel_out_d);
    circle(d = follow_wheel_in_d);   
};
translate(0,0,-(follow_wheel_depth/2+follow_wheel_cover_cap_depth)) 
linear_extrude(follow_wheel_cover_cap_depth) 
difference(){
    circle(d = follow_wheel_out_d);
    circle(d = 608_in_d);
};

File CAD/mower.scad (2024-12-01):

$fn = 256;

width_lemet = 120;
depth_lemet = 20;
height_lemet = 4;

//shaft
height_shaft = 20;
width_shaft_r = 4; 
bore_shaft_r = 1;


// lemet
difference(){
    
difference(){
    translate([0,0,height_lemet/2]) cube([width_lemet, depth_lemet, height_lemet], center= true);
    
        //outside cut-out to provide smooth rotation.
        difference(){
        translate([0,0,height_lemet/2]) cube([width_lemet, depth_lemet, height_lemet], center= true);
        translate([0,0,height_lemet/2]) cylinder(h = height_lemet, r = width_lemet/2, center= true);
        }
}

translate([width_shaft_r,-depth_lemet/2, 0]) 
rotate([atan(height_lemet/depth_lemet),0, 0]) 
cube([width_lemet/2-width_shaft_r, sqrt(depth_lemet^2+width_shaft_r^2), height_lemet]);

rotate([0,0,180])
translate([width_shaft_r,-depth_lemet/2, 0]) 
rotate([atan(height_lemet/depth_lemet),0, 0]) 
cube([width_lemet/2-width_shaft_r, sqrt(depth_lemet^2+width_shaft_r^2), height_lemet]);
}

difference(){
    translate([0 , 0, height_shaft/2]) cylinder(h = height_shaft, r = width_shaft_r, center = true);
    translate([0 , 0, height_shaft/2]) cylinder(h = height_shaft, r = bore_shaft_r, center = true);
}

//create lemet

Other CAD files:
CAD/tank_mower-Track_assemblyPocket007.stl
CAD/To_3D_print/tank_mower-Track_assemblytrack.stl
CAD/3D_printing/tank_mower-Track_assemblybearing002.stl
CAD/To_3D_print/tank_mower-Track_assemblybearing_holder_out_608002.stl
CAD/3-6V_DC-Toy-Motor.step
CAD/3D_printing/Blade.stl
CAD/3D_printing/tank_mower-Track_assemblyExtender.stl
CAD/3D_printing/tank_mower-Track_assemblyM4-Washer001.stl
CAD/3D_printing/tank_mower-Track_assemblyWasher.stl
CAD/3D_printing/tank_mower-chassis_body_V2.stl
CAD/608 ZZ Skateboard Bearing.step
CAD/Chassis.dxf
CAD/TEST_tank_mower.3mf
CAD/To_3D_print/Battery_holder.stl
CAD/To_3D_print/Follower.stl
CAD/To_3D_print/chassis_body_V2.stl
CAD/To_3D_print/puller.stl
CAD/To_3D_print/tank_mower-MowerChamfer012.stl
CAD/To_3D_print/tank_mower-MowerPocket028.stl
CAD/To_3D_print/tank_mower-Track_assemblyWasher.stl
CAD/To_3D_print/tank_mower-chassis_body_V2.stl
CAD/bearing.stl
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

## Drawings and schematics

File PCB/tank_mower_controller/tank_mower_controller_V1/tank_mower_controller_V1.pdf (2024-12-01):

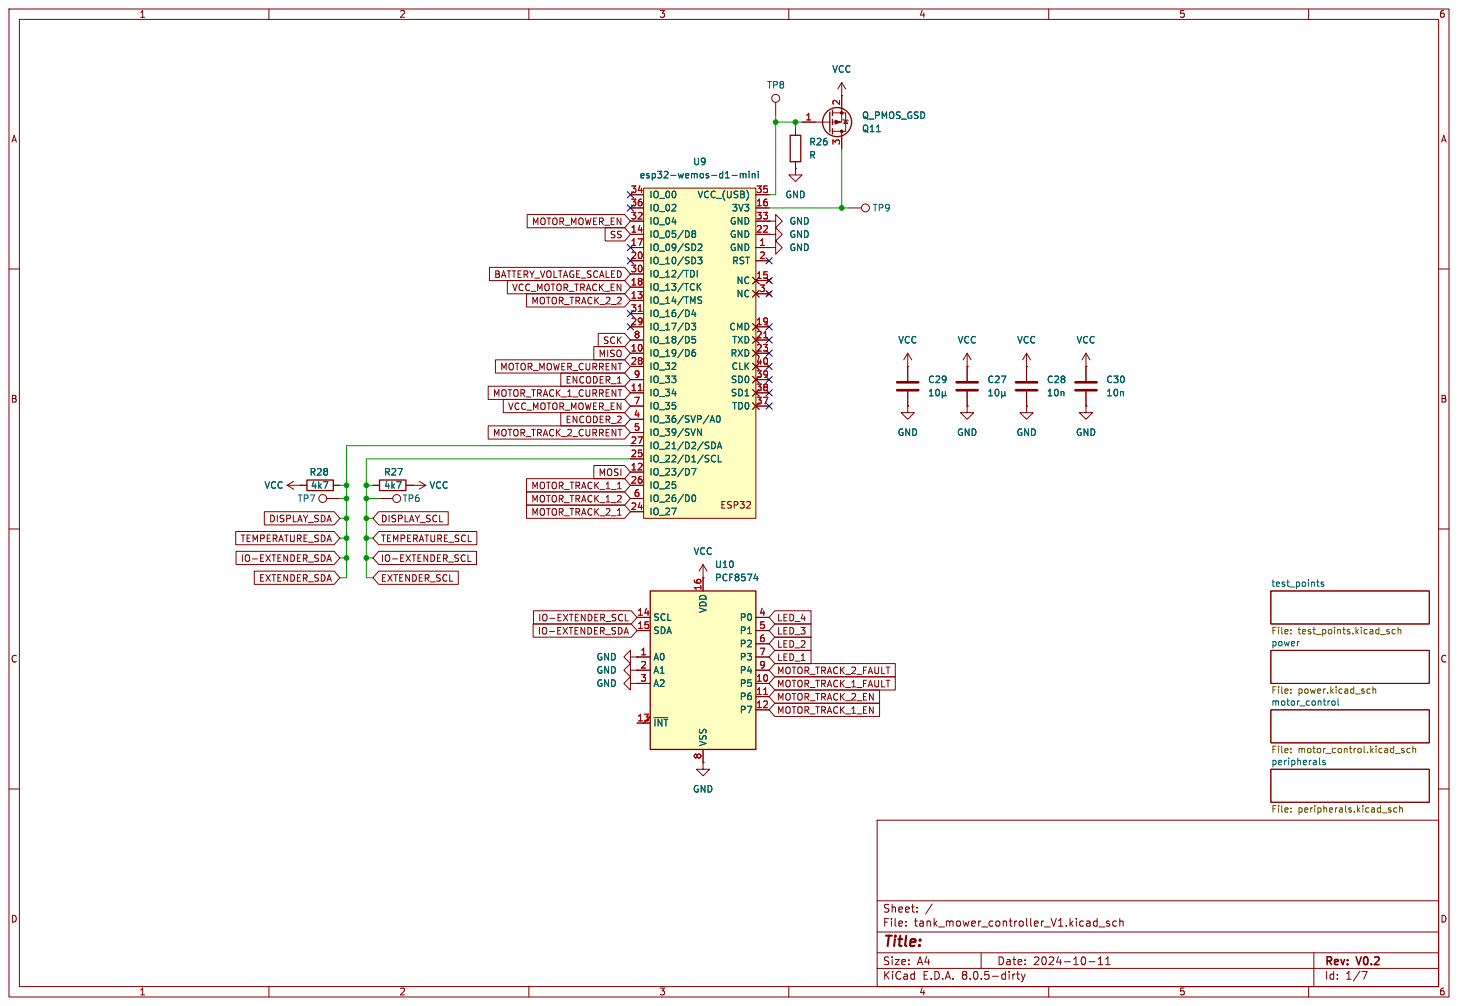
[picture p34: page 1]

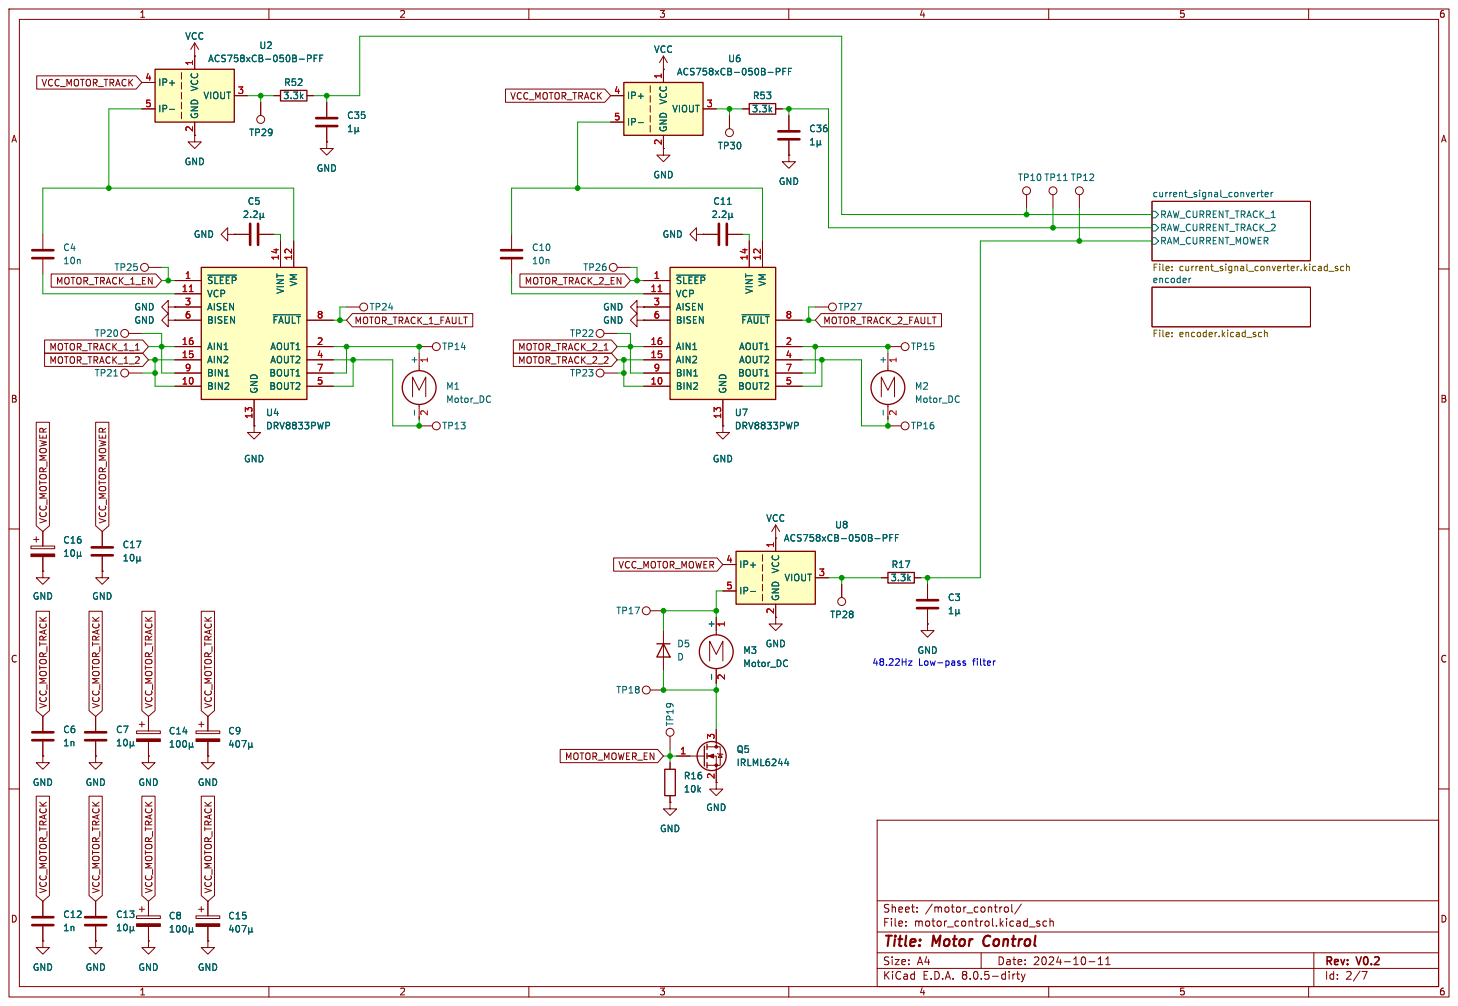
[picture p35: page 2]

-2 M3 Motor_DC GND GND GND GND

Id: 2/7 Title: Motor Control File: motor_control.kicad_sch Sheet: /motor_control/

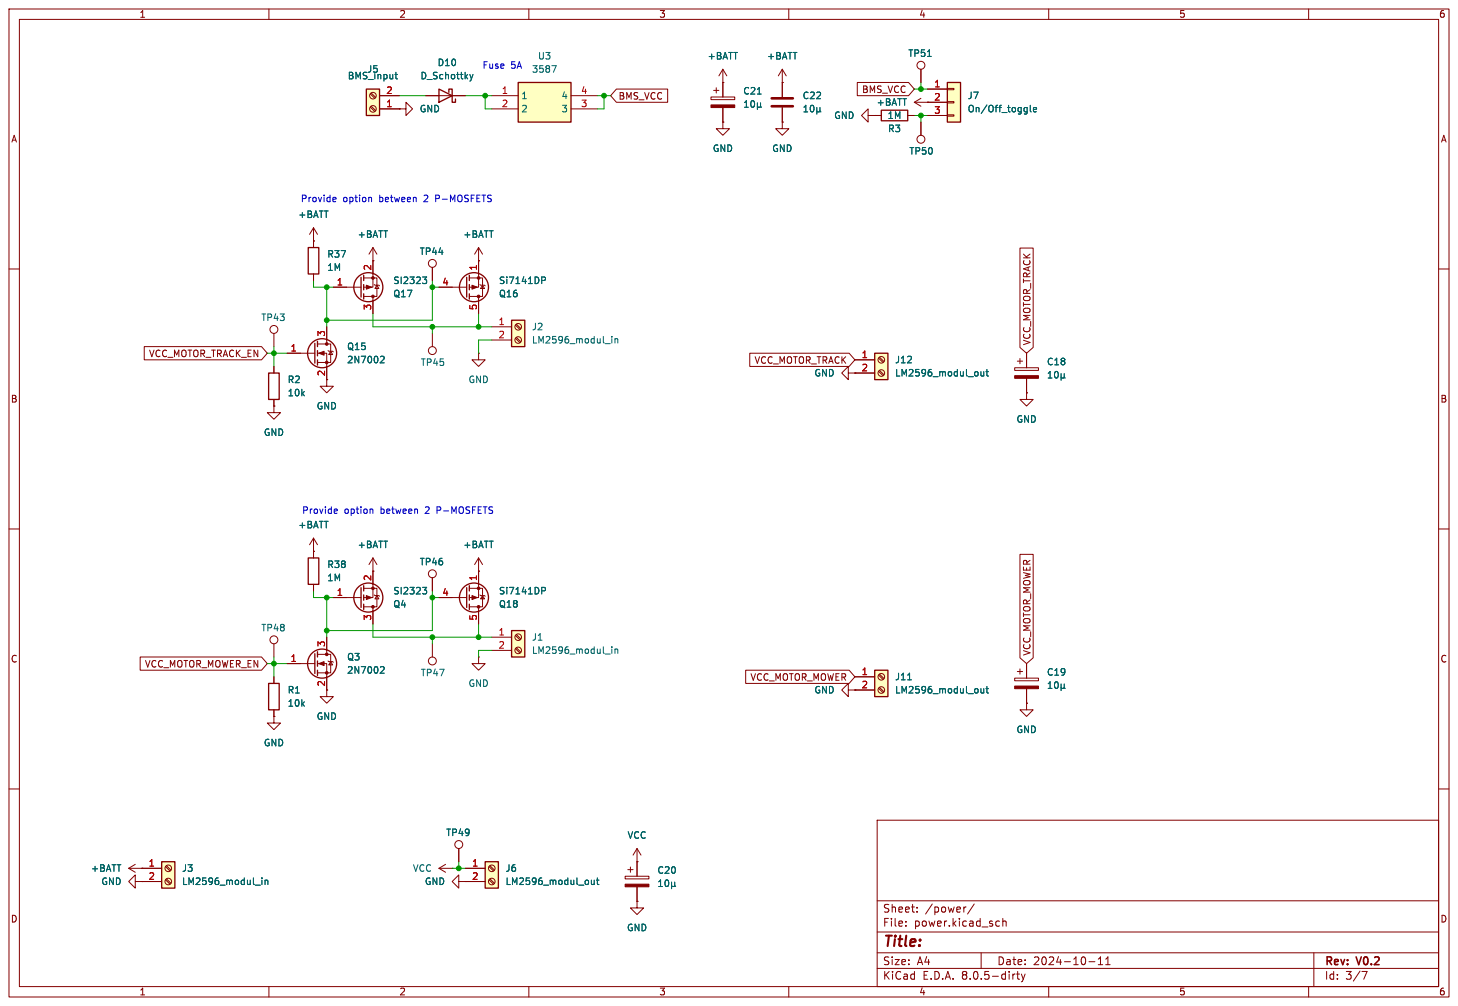
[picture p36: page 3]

+BATT VCC_MOTOR_MOWER
Provide option between 2 P-MOSFETS GND

Provide option between 2 P-MOSFETS
+BATT

Id: 3/7 Title: File: power.kicad_sch Sheet: /power/

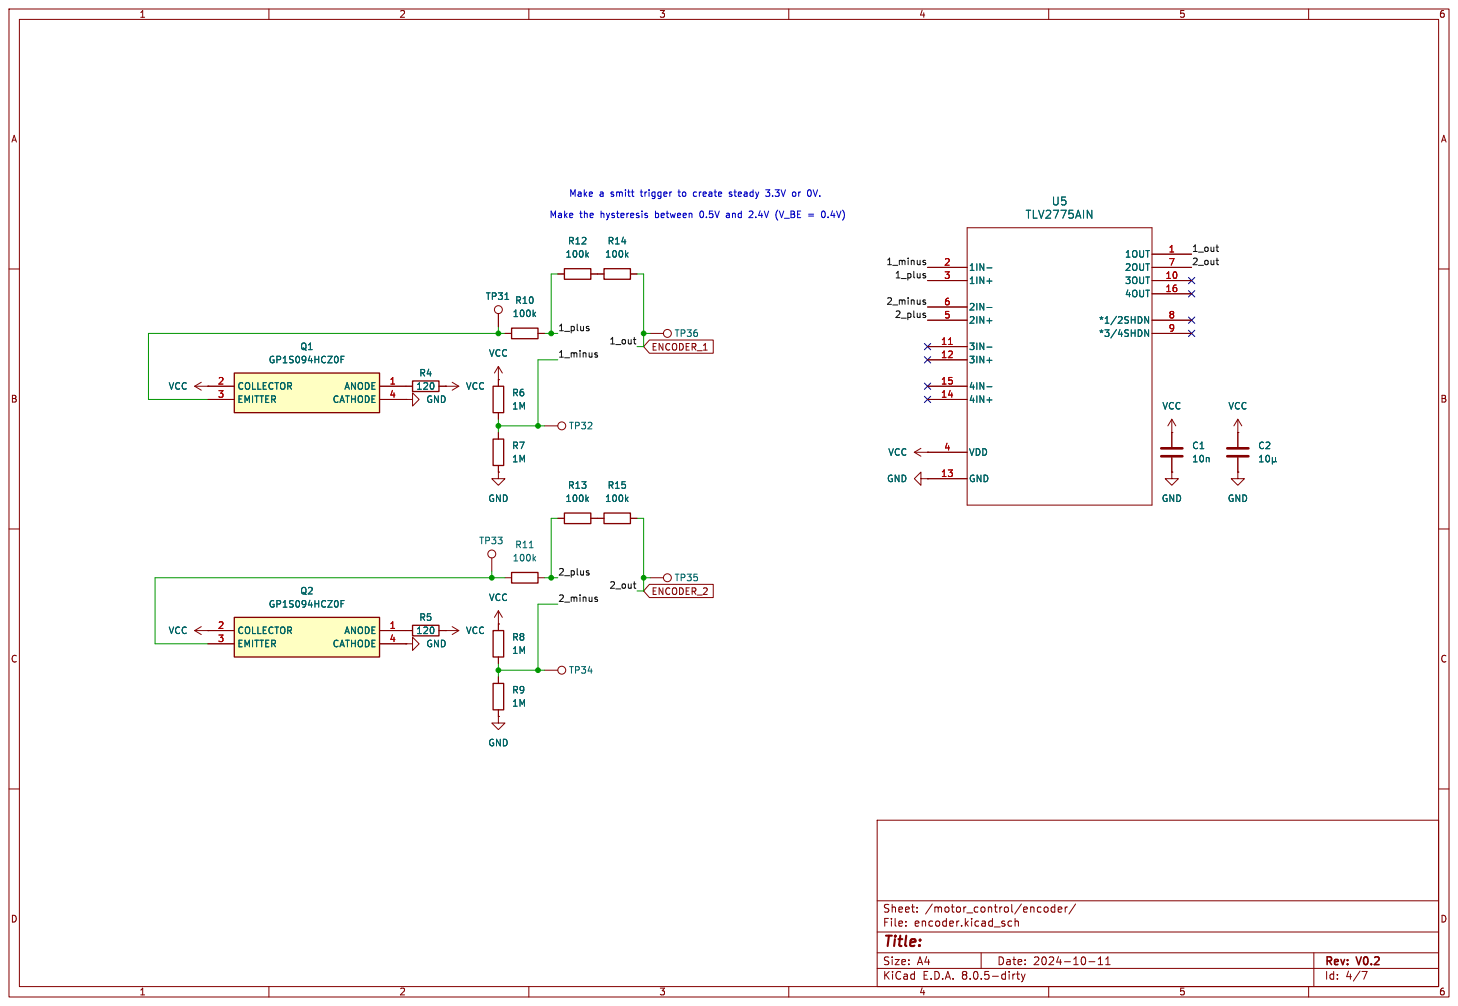
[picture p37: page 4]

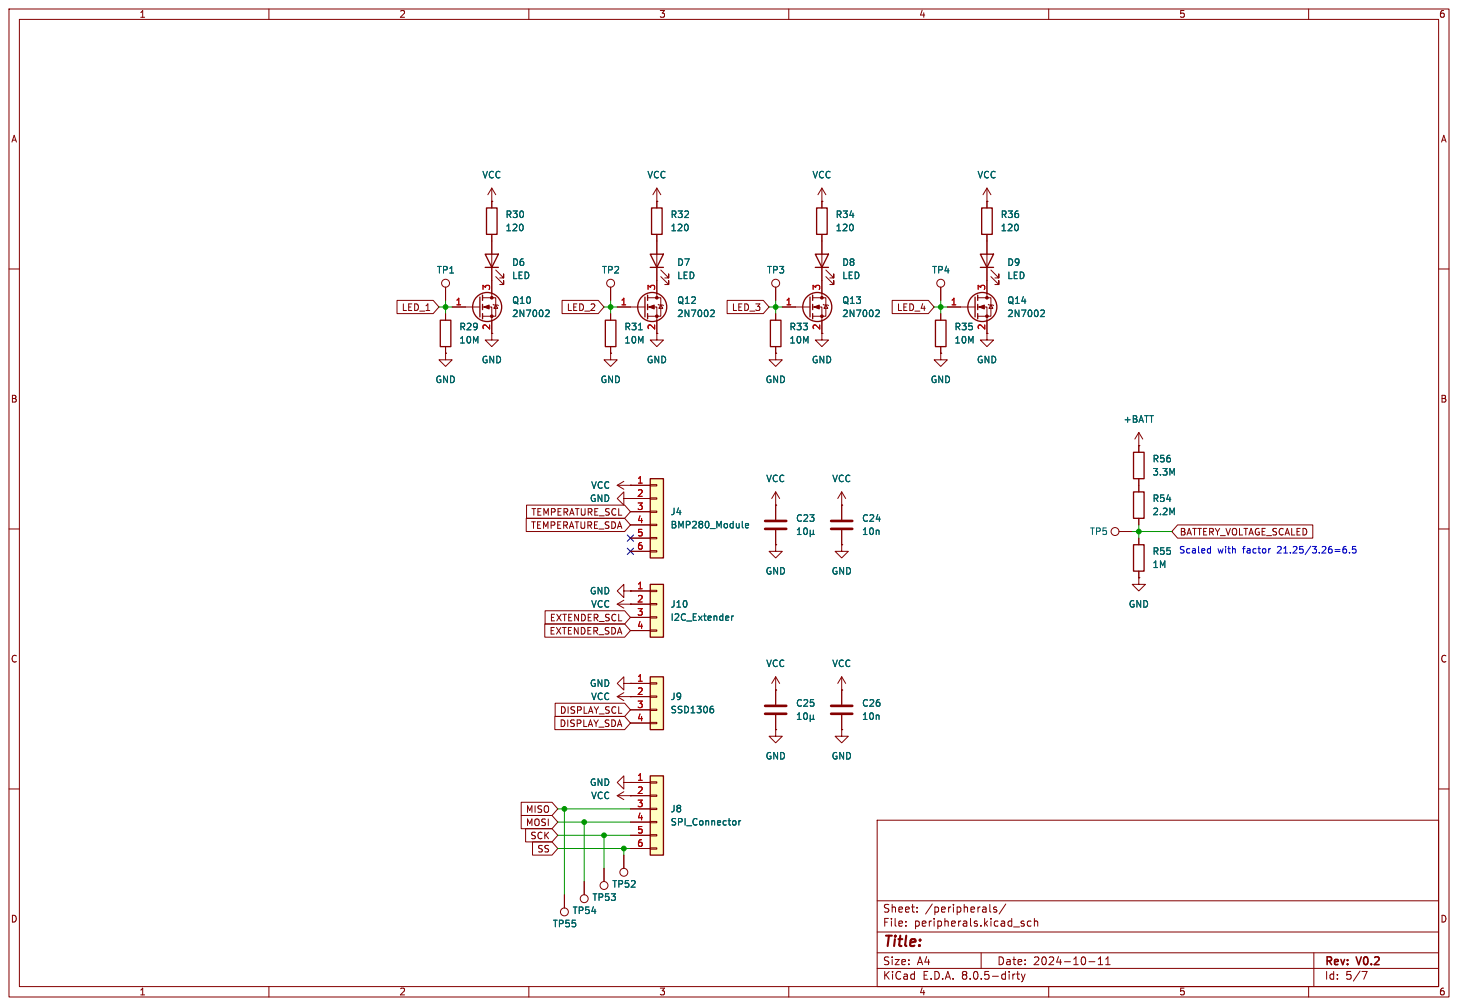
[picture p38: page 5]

Id: 5/7 Title: File: peripherals.kicad_sch Sheet: /peripherals/

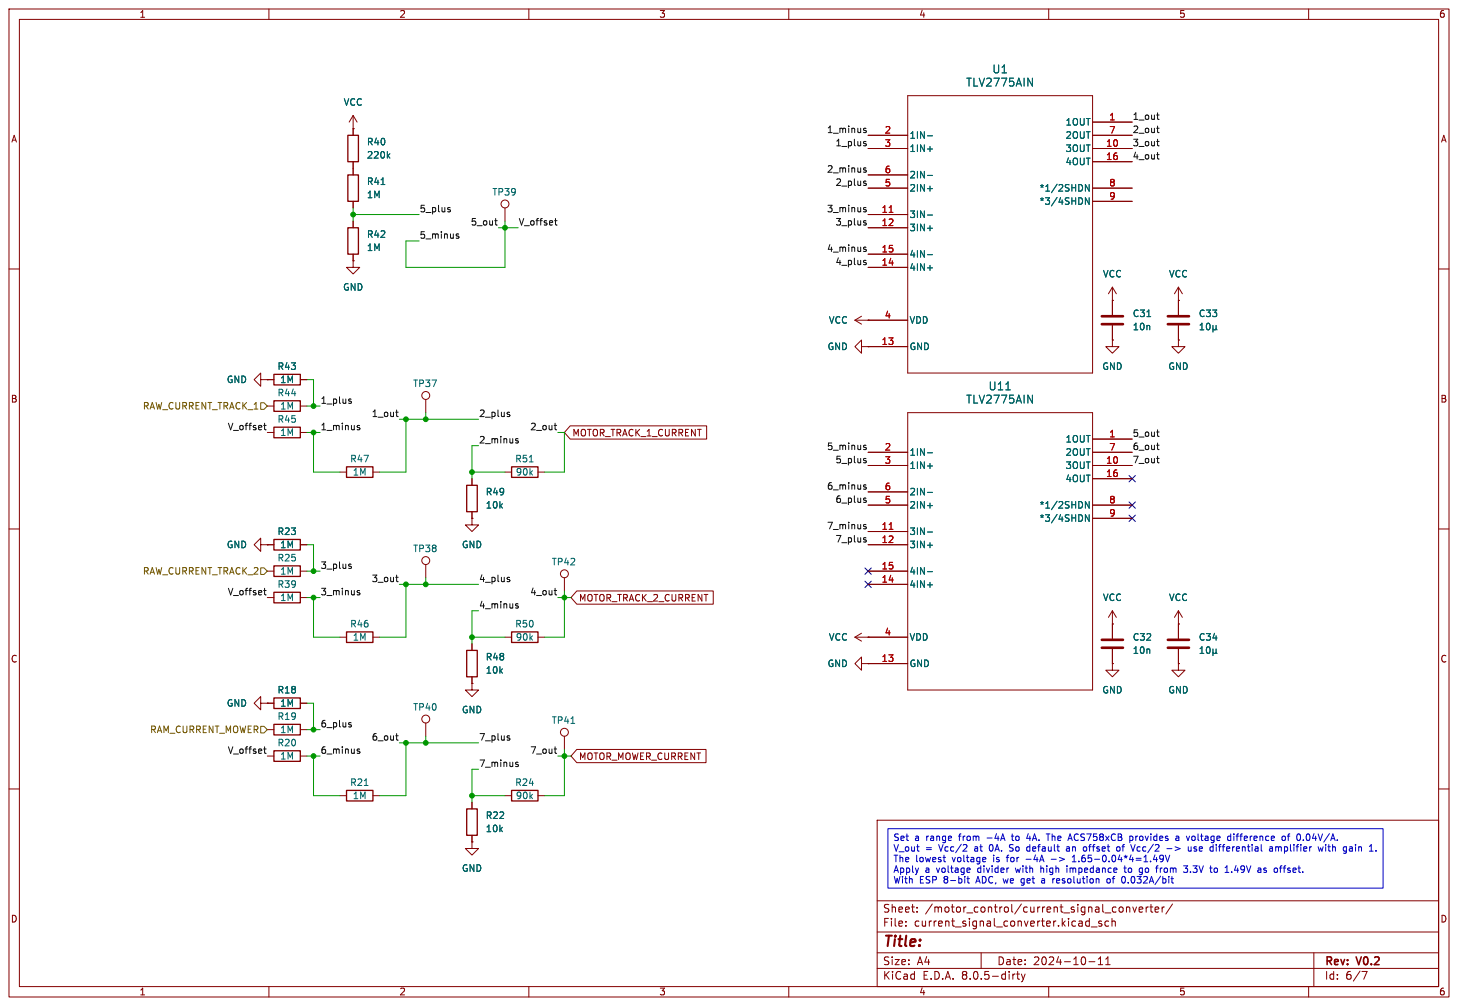
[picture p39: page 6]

Id: 6/7 Title: File: current_signal_converter.kicad_sch Sheet: /motor_control/current_signal_converter/ TP40

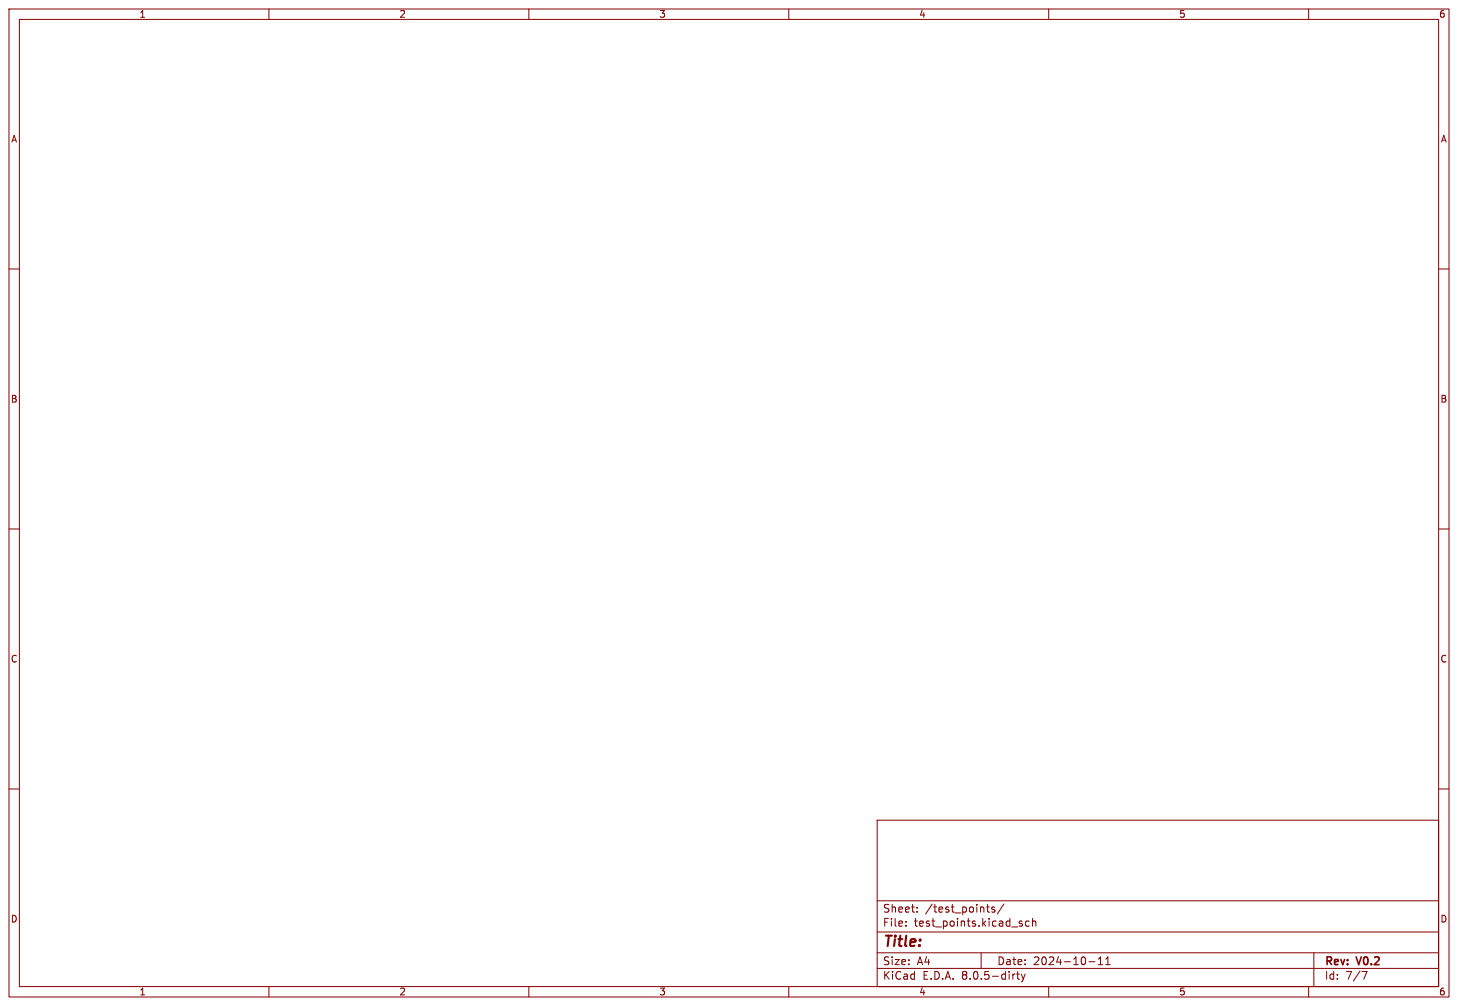
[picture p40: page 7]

Id: 7/7 Title: File: test_points.kicad_sch Sheet: /test_points/

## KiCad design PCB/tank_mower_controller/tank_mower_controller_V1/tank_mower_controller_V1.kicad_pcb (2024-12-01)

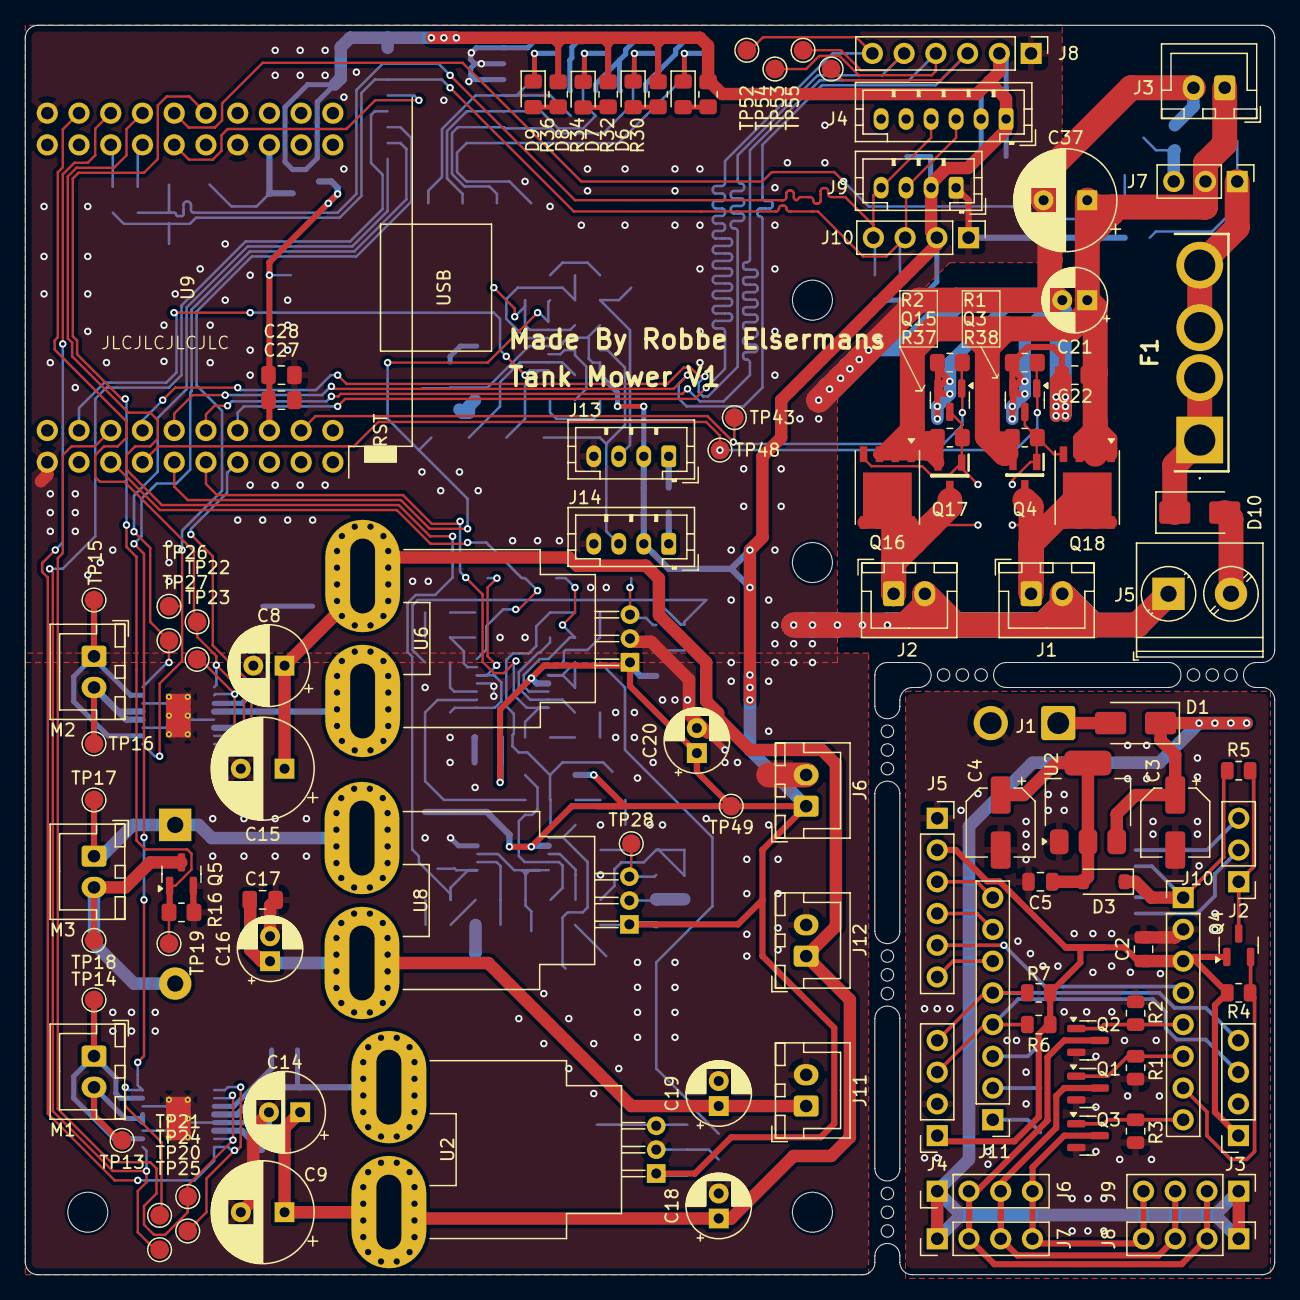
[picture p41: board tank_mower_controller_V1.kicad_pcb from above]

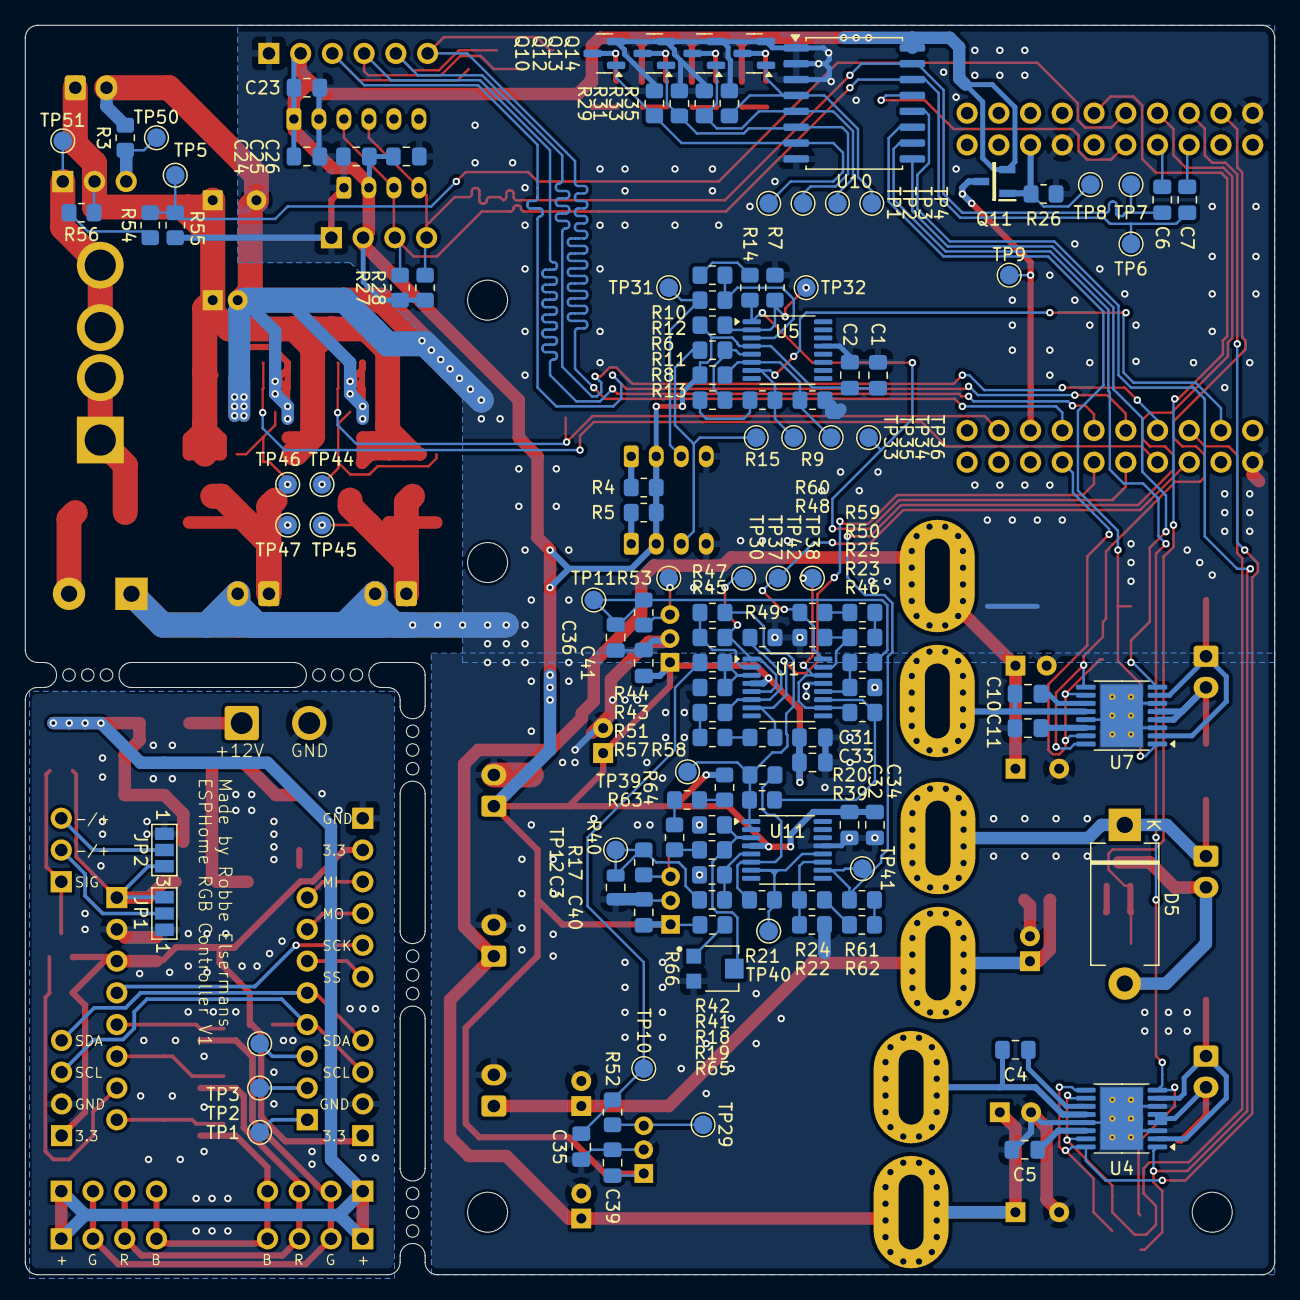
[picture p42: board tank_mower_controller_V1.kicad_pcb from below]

Board: 2 copper layers, 100.0 x 100.0 mm, 237 parts (128 on the bottom side), 106 nets.

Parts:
C1, C4#2, C6, C7, C10, C24, C26, C28, C31, C32: 10n; C_0805_2012Metric_Pad1.18x1.45mm_HandSolder
C2: 10µ; C_0805_2012Metric
C2#2, C17, C22, C23, C25, C27, C33, C34, C39, C40, C41: 10µ; C_0805_2012Metric_Pad1.18x1.45mm_HandSolder
C3, C4: 10µ; CP_Elec_5x5.4
C3#2: 1µ; C_0805_2012Metric
C5: 10n; C_0805_2012Metric
C5#2, C11: 2.2µ; C_0805_2012Metric_Pad1.18x1.45mm_HandSolder
C8, C14: 100µ; CP_Radial_D6.3mm_P2.50mm
C9, C15: 407µ; CP_Radial_D8.0mm_P3.50mm
C16, C18, C19, C20, C21: 10µ; CP_Radial_D5.0mm_P2.00mm
C35, C36: 1µ; C_0805_2012Metric_Pad1.18x1.45mm_HandSolder
C37: 470µ; CP_Radial_D8.0mm_P3.50mm
D1: 1N4009; D_SMA
D3: 1N4819; D_SOD-123
D5: D; D_DO-201_P12.70mm_Horizontal
D6, D7, D8, D9: LED; LED_0805_2012Metric_Pad1.15x1.40mm_HandSolder
D10: D_Schottky; D_SMA
F1: MCCQ-121; MCCQ121
J1, J2, J3: LM2596_modul_in; JST_XH_B2B-XH-A_1x02_P2.50mm_Vertical
J1#2: Jack-DC; SolderWire-1sqmm_1x02_P5.4mm_D1.4mm_OD2.7mm
J2#2: IR-receiver; PinHeader_1x03_P2.54mm_Vertical
J3#2: I2C_expansion; PinSocket_1x04_P2.54mm_Vertical
J4: BMP280_Module; JST_PH_B6B-PH-K_1x06_P2.00mm_Vertical
J4#2: AHT10_module; PinSocket_1x04_P2.54mm_Vertical
J5: BMS_input; TerminalBlock_Phoenix_PT-1,5-2-5.0-H_1x02_P5.00mm_Horizontal
J5#2: SPI_expansion; PinSocket_1x06_P2.54mm_Vertical
J6, J11, J12: LM2596_modul_out; JST_XH_B2B-XH-A_1x02_P2.50mm_Vertical
J6#2, J7#2, J8, J9#2: Conn_01x04; PinHeader_1x04_P2.54mm_Vertical
J7: On/Off_toggle; PinHeader_1x03_P2.54mm_Vertical
J8#2: SPI_Connector; PinHeader_1x06_P2.54mm_Vertical
J9: SSD1306; JST_PH_B4B-PH-K_1x04_P2.00mm_Vertical
J10, J11#2: Conn_01x08; PinHeader_1x08_P2.54mm_Vertical
J10#2: I2C_Extender; PinHeader_1x04_P2.54mm_Vertical
J13, J14: GP1S094HCZ0F; JST_PH_B4B-PH-K_1x04_P2.00mm_Vertical
JP1, JP2: Jumper_3_Open; SolderJumper-3_P1.3mm_Open_Pad1.0x1.5mm_NumberLabels
M1, M2, M3: Motor_DC; JST_XH_B2B-XH-A_1x02_P2.50mm_Vertical
Q1, Q2, Q3, Q4: AO3400A; SOT-23
Q3#2, Q10, Q12, Q13, Q14, Q15: 2N7002; SOT-23
Q4#2, Q11, Q17: SI2323; SOT95P237X112-3N
Q5: IRLML6244; SOT-23
Q16, Q18: Si7141DP; PowerPAK_SO-8_Single
R1, R2, R16, R22, R48, R49, R58, R60, R62: 10k; R_0805_2012Metric_Pad1.20x1.40mm_HandSolder
R1#2, R2#2, R3: 100k; R_0805_2012Metric
R3#2, R6#2, R7#2, R8, R9, R18, R19, R20, R21, R23, R25, R37, R38, R39, R41, R42, R43, R44, R45, R46, R47, R55: 1M; R_0805_2012Metric_Pad1.20x1.40mm_HandSolder
R4, R5: 10k; R_0805_2012Metric
R4#2, R5#2, R30, R32, R34, R36: 120; R_0805_2012Metric_Pad1.20x1.40mm_HandSolder
R6, R7: 4k7; R_0805_2012Metric
R10, R11, R12, R13, R14, R15, R40, R63: 100k; R_0805_2012Metric_Pad1.20x1.40mm_HandSolder
R17, R52, R53: 3.3k; R_0805_2012Metric_Pad1.20x1.40mm_HandSolder
R24, R50, R51: 68k; R_0805_2012Metric_Pad1.20x1.40mm_HandSolder
R26: R; R_0805_2012Metric_Pad1.20x1.40mm_HandSolder
R27, R28: 4k7; R_0805_2012Metric_Pad1.20x1.40mm_HandSolder
R29, R31, R33, R35: 10M; R_0805_2012Metric_Pad1.20x1.40mm_HandSolder
R54: 2.2M; R_0805_2012Metric_Pad1.20x1.40mm_HandSolder
R56: 3.3M; R_0805_2012Metric_Pad1.20x1.40mm_HandSolder
R57, R59, R61: 12k; R_0805_2012Metric_Pad1.20x1.40mm_HandSolder
R64, R65: 15k; R_0805_2012Metric_Pad1.20x1.40mm_HandSolder
R66: 1M; TRIM_TC33X-2-105E
TP1, TP1#2, TP2, TP2#2, TP3, TP3#2, TP4, TP5, TP6, TP7, TP8, TP9, TP10, TP11, TP12, TP13, TP14, TP15, TP16, TP17, TP18, TP19, TP20, TP21, TP22, TP23, TP24, TP25, TP26, TP27, TP28, TP29, TP30, TP31, TP32, TP33, TP34, TP35, TP36, TP37, TP38, TP39, TP40, TP41, TP42, TP43, TP44, TP45, TP46, TP47, TP48, TP49, TP50, TP51, TP52, TP53, TP54, TP55: TestPoint; TestPoint_Pad_D1.5mm
U1, U5, U11: TLV2775AIN; TSSOP-16_4.4x5mm_P0.65mm
U2, U6, U8: ACS758xCB-050B-PFF; Allegro_CB_PFF
U2#2: AMS1117-5.0; SOT-223-3_TabPin2
U4, U7: DRV8833PWP; HTSSOP-16-1EP_4.4x5mm_P0.65mm_EP3.4x5mm_Mask2.46x2.31mm_The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
U9: esp32-wemos-d1-mini
U10: PCF8574; SOIC-16W_7.5x10.3mm_P1.27mm

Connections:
+BATT: C21.1, C22.1, C37.1, J3.1, J7.2, Q4#2.2 (S), Q16.1 (S), Q16.2 (S), Q16.3 (S), Q17.2 (S), Q18.1 (S), Q18.2 (S), Q18.3 (S), R37.1, R38.1, R56.1
/motor_control/current_signal_converter/1_minus: R45.2, R47.1, U1.2 (1IN-)
/motor_control/current_signal_converter/1_out: R47.2, TP37.1, U1.1 (1OUT), U1.5 (2IN+)
/motor_control/current_signal_converter/1_plus: R43.2, R44.2, U1.3 (1IN+)
/motor_control/current_signal_converter/2_minus: R49.1, R51.1, U1.6 (2IN-)
/motor_control/current_signal_converter/3_minus: R39.2, R46.1, U1.11 (3IN-)
/motor_control/current_signal_converter/3_out: R46.2, TP38.1, U1.10 (3OUT), U1.14 (4IN+)
/motor_control/current_signal_converter/3_plus: R23.2, R25.2, U1.12 (3IN+)
/motor_control/current_signal_converter/4_minus: R48.1, R50.1, U1.15 (4IN-)
/motor_control/current_signal_converter/5_minus: R20.1, R39.1, R45.1, TP39.1, U11.1 (1OUT), U11.2 (1IN-)
/motor_control/current_signal_converter/5_plus: R41.2, R42.1, R66.2, U11.3 (1IN+)
/motor_control/current_signal_converter/6_minus: R20.2, R21.1, U11.6 (2IN-)
/motor_control/current_signal_converter/6_out: R21.2, TP40.1, U11.7 (2OUT), U11.12 (3IN+)
/motor_control/current_signal_converter/6_plus: R18.2, R19.2, U11.5 (2IN+)
/motor_control/current_signal_converter/7_minus: R22.1, R24.1, U11.11 (3IN-)
/motor_control/current_signal_converter/RAM_CURRENT_MOWER: C3#2.1, R17.2, R19.1, TP12.1
/motor_control/current_signal_converter/RAW_CURRENT_TRACK_1: C35.1, R44.1, R52.2, TP10.1
/motor_control/current_signal_converter/RAW_CURRENT_TRACK_2: C36.1, R25.1, R53.2, TP11.1
/motor_control/encoder/1_minus: R6#2.2, R7#2.1, TP32.1, U5.2 (1IN-)
/motor_control/encoder/1_plus: R10.2, R12.1, U5.3 (1IN+)
/motor_control/encoder/2_minus: R8.2, R9.1, TP34.1, U5.6 (2IN-)
/motor_control/encoder/2_plus: R11.2, R13.1, U5.5 (2IN+)
BATTERY_VOLTAGE_SCALED: R54.2, R55.1, TP5.1, U9.30 (IO_12/TDI)
BMS_VCC: F1.3, F1.4, J7.1, TP51.1
DISPLAY_SCL: C7.1, J4.3, J9.3, J10#2.3, R27.2, TP6.1, U10.14 (SCL)
DISPLAY_SDA: C6.1, J4.4, J9.4, J10#2.4, R28.2, TP7.1, U10.15 (SDA)
ENCODER_1: R14.2, TP36.1, U5.1 (1OUT), U9.9 (IO_33)
ENCODER_2: R15.2, TP35.1, U5.7 (2OUT), U9.4 (IO_36/SVP/A0)
GND: C1.2, C2.2, C2#2.2, C3.2, C3#2.2, C4.2, C5.2, C5#2.1, C8.2, C9.2, C11.1, C14.2, C15.2, C16.2, C17.2, C18.2, C19.2, C20.2, C21.2, C22.2, C23.2, C24.2, C25.2, C26.2, C27.2, C28.2, C31.2, C32.2, C33.2, C34.2, C35.2, C36.2, C37.2, C39.2, C40.2, C41.2, J1.2, J1#2.2, J2.2, J3.2, J3#2.2, J4.2, J4#2.2, J5.1, J5#2.1, J6.2, J8#2.1, J9.1, J10.2, J10#2.1, J11.2, J12.2, J13.4, J14.4, JP1.1 (A), JP2.1 (A), Q1.2 (S), Q2.2 (S), Q3.2 (S), Q3#2.2 (S), Q5.2 (S), Q10.2 (S), Q12.2 (S), Q13.2 (S), Q14.2 (S), Q15.2 (S), R1.2, R1#2.2, R2.2, R2#2.2, R3.2, R3#2.1, R7#2.2, R9.2, R16.2, R18.1, R22.2, R23.1, R26.2, R29.2, R31.2, R33.2, R35.2, R42.2, R43.1, R48.2, R49.2, R55.2, R66.3, U1.13 (GND), U2.2 (GND), U2#2.1 (GND), U4.3 (AISEN), U4.6 (BISEN), U4.13 (GND), U4.17 (GND), U5.13 (GND), U6.2 (GND), U7.3 (AISEN), U7.6 (BISEN), U7.13 (GND), U7.17 (GND), U8.2 (GND), U9.1 (GND), U9.22 (GND), U9.33 (GND), U10.1 (A0), U10.2 (A1), U10.3 (A2), U10.8 (VSS), U11.13 (GND)
IO-EXTENDER_INTERUPT: U9.29 (IO_17/D3), U10.13 (~INT)
LED_1: Q10.1 (G), R29.1, TP1#2.1, U10.7 (P3)
LED_2: Q12.1 (G), R31.1, TP2.1, U10.6 (P2)
LED_3: Q13.1 (G), R33.1, TP3.1, U10.5 (P1)
LED_4: Q14.1 (G), R35.1, TP4.1, U10.4 (P0)
MISO: J8#2.3, TP55.1, U9.10 (IO_19/D6)
MOSI: J8#2.4, TP54.1, U9.12 (IO_23/D7)
MOTOR_MOWER_CURRENT: R62.2, TP41.1, U9.28 (IO_32), U11.10 (3OUT)
MOTOR_MOWER_EN: Q5.1 (G), R16.1, TP19.1, U9.32 (IO_04)
MOTOR_TRACK_1_1: TP20.1, U4.9 (BIN1), U4.16 (AIN1), U9.26 (IO_25)
MOTOR_TRACK_1_2: TP21.1, U4.10 (BIN2), U4.15 (AIN2), U9.6 (IO_26/D0)
MOTOR_TRACK_1_CURRENT: R58.2, U1.7 (2OUT), U9.11 (IO_34)
MOTOR_TRACK_1_EN: TP25.1, U4.1 (~SLEEP), U10.12 (P7)
MOTOR_TRACK_1_FAULT: TP24.1, U4.8 (~FAULT), U10.10 (P5)
MOTOR_TRACK_2_1: TP22.1, U7.9 (BIN1), U7.16 (AIN1), U9.24 (IO_27)
MOTOR_TRACK_2_2: TP23.1, U7.10 (BIN2), U7.15 (AIN2), U9.13 (IO_14/TMS)
MOTOR_TRACK_2_CURRENT: R60.2, TP42.1, U1.16 (4OUT), U9.5 (IO_39/SVN)
MOTOR_TRACK_2_EN: TP26.1, U7.1 (~SLEEP), U10.11 (P6)
MOTOR_TRACK_2_FAULT: TP27.1, U7.8 (~FAULT), U10.9 (P4)
unnamed: D5.2 (A), M3.2 (-), Q5.3 (D), TP18.1
unnamed: D5.1 (K), M3.1 (+), TP17.1, U8.4 (IP+)
unnamed: D6.2 (A), R30.2
unnamed: D6.1 (K), Q10.3 (D)
unnamed: D7.2 (A), R32.2
unnamed: D7.1 (K), Q12.3 (D)
unnamed: D8.2 (A), R34.2
unnamed: D8.1 (K), Q13.3 (D)
unnamed: D9.2 (A), R36.2
unnamed: D9.1 (K), Q14.3 (D)
unnamed: D10.2 (A), J5.2
unnamed: D10.1 (K), F1.1, F1.2
unnamed: J1.1, Q4#2.3 (D), Q18.5 (D), TP47.1
unnamed: J2.1, J2#2.1, Q4.3 (D), Q16.5 (D), Q17.3 (D), R5.2, TP45.1
unnamed: J7.3, R3#2.2, TP50.1
unnamed: J13.1, R4#2.1
unnamed: J13.3, R10.1, TP31.1
unnamed: J14.1, R5#2.1
unnamed: J14.3, R11.1, TP33.1
unnamed: M1.1 (+), TP14.1, U4.2 (AOUT1), U4.7 (BOUT1)
unnamed: M1.2 (-), TP13.1, U4.4 (AOUT2), U4.5 (BOUT2)
unnamed: M2.1 (+), TP15.1, U7.2 (AOUT1), U7.7 (BOUT1)
unnamed: M2.2 (-), TP16.1, U7.4 (AOUT2), U7.5 (BOUT2)
unnamed: C27.1, C28.1, Q11.3 (D), TP9.1, U9.16 (3V3)
unnamed: Q11.1 (G), R26.1, TP8.1, U9.35 (VCC_(USB))
unnamed: Q15.3 (D), Q16.4 (G), Q17.1 (G), R37.2, TP44.1
unnamed: Q3#2.3 (D), Q4#2.1 (G), Q18.4 (G), R38.2, TP46.1
unnamed: R12.2, R14.1
unnamed: R13.2, R15.1
unnamed: R24.2, R61.1
unnamed: R40.1, R63.2
unnamed: R40.2, R41.1
unnamed: R50.2, R59.1
unnamed: R51.2, R57.1
unnamed: R54.1, R56.2
unnamed: R57.2, R58.1
unnamed: R59.2, R60.1
unnamed: R61.2, R62.1
unnamed: R63.1, R64.2
unnamed: R65.2, R66.1
unnamed: C4#2.2, U2.4 (IP+), U4.12 (VM)
unnamed: R52.1, TP29.1, U2.3 (VIOUT)
unnamed: C4#2.1, U4.11 (VCP)
unnamed: C5#2.2, U4.14 (VINT)
unnamed: C10.2, U6.5 (IP-), U7.12 (VM)
unnamed: R53.1, TP30.1, U6.3 (VIOUT)
unnamed: C10.1, U7.11 (VCP)
unnamed: C11.2, U7.14 (VINT)
unnamed: R17.1, TP28.1, U8.3 (VIOUT)
unnamed: C6.2, U9.27 (IO_21/D2/SDA)
unnamed: C7.2, U9.25 (IO_22/D1/SCL)
SCK: J8#2.5, TP53.1, U9.8 (IO_18/D5)
SS: J8#2.6, TP52.1, U9.14 (IO_05/D8)
VCC: C1.1, C2.1, C2#2.1, C20.1, C23.1, C24.1, C25.1, C26.1, C31.1, C32.1, C33.1, C34.1, C39.1, C40.1, C41.1, J3#2.1, J4.1, J4#2.1, J5#2.2, J6.1, J8#2.2, J9.2, J10.3, J10#2.2, J13.2, J14.2, Q4.1 (G), Q11.2 (S), R4.1, R4#2.2, R5#2.2, R6.1, R6#2.1, R7.1, R8.1, R27.1, R28.1, R30.1, R32.1, R34.1, R36.1, R64.1, R65.1, TP49.1, U1.4 (VDD), U2.1 (VCC), U5.4 (VDD), U6.1 (VCC), U8.1 (VCC), U10.16 (VDD), U11.4 (VDD)
VCC_MOTOR_MOWER: C16.1, C17.1, C19.1, J11.1, U8.5 (IP-)
VCC_MOTOR_MOWER_EN: Q3#2.1 (G), R1.1, TP48.1, U9.7 (IO_35)
VCC_MOTOR_TRACK: C8.1, C9.1, C14.1, C15.1, C18.1, J12.1, U2.5 (IP-), U6.4 (IP+)
VCC_MOTOR_TRACK_EN: Q15.1 (G), R2.1, TP43.1, U9.18 (IO_13/TCK)

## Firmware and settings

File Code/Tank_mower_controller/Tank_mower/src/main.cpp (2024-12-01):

#include <Arduino.h>
#include "main.h"
// #include <Adafruit_BMP280.h>
#include <Wire.h>
#include <Adafruit_GFX.h>
#include <Adafruit_SSD1306.h>
#include "PCF8574.h"
#include "ESP32MotorControl.h" 	// https://github.com/JoaoLopesF/ESP32MotorControl

#define DEBUG

#include <BluetoothSerial.h>

//Battery voltage
float voltage_battery = 0.0; // In V
const float delta_v = 0.000805664;
const double scaler_battery_voltage = 12; //6.5

//Currents
float current_mower = 0.0;    // In mA
float current_track_1 = 0.0;  // In mA
float current_track_2 = 0.0;  // In mA
const float delta_i = 0.0021416; //delta_v/i_res
const float mid_current = 4096/2.0 * delta_i;

//State variable
float round_trip_time;

//Bluetooth commands and placeholders
BluetoothSerial SerialBT;
uint8_t read_char[8];
uint8_t command_index_end = 0;
const uint8_t FORWARD_COMMAND = 'F';
const uint8_t REVERSE_COMMAND = 'B';
const uint8_t RIGHT_COMMAND = 'R';
const uint8_t LEFT_COMMAND = 'L';
const uint8_t MOWER_COMMAND = 'M';

//Boolean locations
#define BOOL_FORWARD 0
#define BOOL_REVERSE 1
#define BOOL_LEFT 2
#define BOOL_RIGHT 3

//Boolean locations
#define BOOL_FORWARD_ACTIVE 4
#define BOOL_REVERSE_ACTIVE 5
#define BOOL_LEFT_ACTIVE 6
#define BOOL_RIGHT_ACTIVE 7

//Boolean locations
#define BOOL_MOWER 0
#define BOOL_MOWER_RAMP_DONE 1
#define BOOL_MOWER_ACTIVE 4

////Boolean containers
uint8_t bool_holder_1 = 0b00000000;
uint8_t bool_holder_2 = 0b00000000;

//Time of command execution
#define FORWARD_TIME 1000
#define REVERSE_TIME 1000
#define LEFT_TIME 500
#define RIGHT_TIME 500
#define MOWER_RAMP_TIME 10
#define MOWER_FALL_TIME 1

long forward_timer;
long left_timer;
long right_timer;
long reverse_timer;
long ramp_timer;

#define MOWER_MAX_VALUE 255
uint8_t mower_value;


//Library Motor control
ESP32MotorControl MotorControl = ESP32MotorControl();

//Library IO expansion Module
TwoWire I2Ctwo = TwoWire(1); //Default on 21 and 22
PCF8574 pcf8574(&I2Ctwo, 0x20); 

//OLED display
Adafruit_SSD1306 display = Adafruit_SSD1306(128, 64, &Wire, -1);
#define SCREEN_UPDATE_TIME 100
long screen_update_timer;

void setup()
{
  // put your setup code here, to run once:
  Serial.begin(115200); // make sure your Serial Monitor is also set at this baud rate.
  SerialBT.begin("tankBot");

  //attach the motors
  MotorControl.attachMotors(MOTOR_TRACK_1_1, MOTOR_TRACK_1_2, MOTOR_TRACK_2_2, MOTOR_TRACK_2_1); //1.1 1.2 2.2 2.1

  // pinMode(MOTOR_TRACK_1_1, OUTPUT);
  // pinMode(MOTOR_TRACK_1_2, OUTPUT);
  // pinMode(MOTOR_TRACK_2_1, OUTPUT);
  // pinMode(MOTOR_TRACK_2_2, OUTPUT);

  display.begin(SSD1306_SWITCHCAPVCC, 0x3C);
  delay(2000);
  display.setRotation(2); //Rotate 180°

  //Add and enable VCC of motors
  // pinMode(VCC_MOTOR_MOWER_EN, OUTPUT);
  pinMode(VCC_MOTOR_TRACK_EN, OUTPUT);
  // digitalWrite(VCC_MOTOR_MOWER_EN, HIGH);
  digitalWrite(VCC_MOTOR_TRACK_EN, HIGH);

  //Add current pins
  pinMode(MOTOR_CURRENT_MOWER, INPUT);
  pinMode(MOTOR_TRACK_1_CURRENT, INPUT);
  pinMode(MOTOR_TRACK_2_CURRENT, INPUT);

  //Add mower motor
  pinMode(MOTOR_MOWER_EN, OUTPUT);  

  pcf8574.begin();
  delay(100);

  pcf8574.pinMode(LED_1, OUTPUT);
  pcf8574.pinMode(LED_2, OUTPUT);
  pcf8574.pinMode(LED_3, OUTPUT);
  pcf8574.pinMode(LED_4, OUTPUT);
  pcf8574.pinMode(MOTOR_TRACK_1_EN, OUTPUT);
  pcf8574.pinMode(MOTOR_TRACK_2_EN, OUTPUT);
  pcf8574.pinMode(MOTOR_TRACK_1_FAULT, INPUT);
  pcf8574.pinMode(MOTOR_TRACK_2_FAULT, INPUT);
  
  delay(1000);
  
  pcf8574.digitalWrite(MOTOR_TRACK_2_EN, HIGH);
  pcf8574.digitalWrite(MOTOR_TRACK_1_EN, HIGH);

  // LED fancy thing
  pcf8574.digitalWrite(LED_1, HIGH);
  delay(500);
  pcf8574.digitalWrite(LED_1, LOW);
  pcf8574.digitalWrite(LED_2, HIGH);
  delay(500);
  pcf8574.digitalWrite(LED_2, LOW);
  pcf8574.digitalWrite(LED_3, HIGH);
  delay(500);
  pcf8574.digitalWrite(LED_3, LOW);
  pcf8574.digitalWrite(LED_4, HIGH);
  delay(500);
  pcf8574.digitalWrite(LED_4, LOW);
}

void loop()
{
  float time = millis();
  readCommand();
  // Process the command
  handleCommand();
  //run command  
  executeCommand();

  //Read current
  calculateCurrent(MOTOR_CURRENT_MOWER, &current_mower);
  calculateCurrent(MOTOR_TRACK_1_CURRENT, &current_track_1);
  calculateCurrent(MOTOR_TRACK_2_CURRENT, &current_track_2);

  calculateVoltage(BATTERY_VOLTAGE_SCALED, &voltage_battery);
  // Display the used command on the OLED
  displayData();

  round_trip_time = (millis() - time);
}

void displayData()
{
  if ((millis() - screen_update_timer) > SCREEN_UPDATE_TIME){
    display.clearDisplay();
    display.setTextSize(1,1);
    display.setTextColor(SSD1306_WHITE);
    display.setCursor(0,1);
    display.println("Hello Tank Mower");
    // display.println("Welcome!");
    display.print("trip time:");
    display.print(round_trip_time);
    display.println("ms");
    display.print("Command ");
    display.println(bool_holder_1, BIN);
    
    display.print("MI: ");
    display.print(current_mower);
    display.print(" mA, ");

    display.print("T1I: ");
    display.print(current_track_1);
    display.print(" mA, ");

    display.print("T2I: ");
    display.print(current_track_2);
    display.print(" mA, ");

    display.print("Vcc: ");
    display.print(voltage_battery);
    display.print(" V, ");
    
    display.setCursor(0,0);
    display.display();
    screen_update_timer = millis();
  }
}

void calculateVoltage(uint8_t pin, float* voltage)
{
  int analog_value = analogRead(pin);
  *voltage = analog_value*delta_v*scaler_battery_voltage;
  Serial.printf("raw:%d, cal: %f \r\n", analog_value, *voltage);
}

void calculateCurrent(uint8_t pin, float* current)
{
  int analog_current = 0;
  int cycles = 50;

  for(uint8_t i = 0; i < cycles; i++)
  {
    analog_current += analogRead(pin);
  }

  analog_current /= cycles;

  *current = (float)(analog_current*delta_i)-mid_current;
  if (*current < 0){
    *current = 0;
  }
  *current *= 1000; //Set to mA.
}

void readCommand()
{
  while (SerialBT.available())
  {
    for (uint8_t i = 0; i < 8; i++)
    {
      read_char[i] = SerialBT.read();
      if (read_char[i] == (uint8_t)13)
      {
        // A new command has entered the building!
        command_index_end = i - 1;
      }
    }
  }

  // Run the bot if a command has been received.

  // Forward is executed 1 second
  if (read_char[command_index_end] == FORWARD_COMMAND)
  {
    setBool(&bool_holder_1, (uint8_t)BOOL_FORWARD);
  }

  // Reverse is executed 1 second

  if (read_char[command_index_end] == REVERSE_COMMAND)
  {
    setBool(&bool_holder_1, (uint8_t)BOOL_REVERSE);
  }

  // Left is executed 0.2 second

  if (read_char[command_index_end] == LEFT_COMMAND)
  {
    setBool(&bool_holder_1, (uint8_t)BOOL_LEFT);
  }
  // Right is executed 0.2 second

  if (read_char[command_index_end] == RIGHT_COMMAND)
  {
    setBool(&bool_holder_1, (uint8_t)BOOL_RIGHT);
  }

  if (read_char[command_index_end] == MOWER_COMMAND)
  {
    setBool(&bool_holder_2, (uint8_t)BOOL_MOWER);
  }

  read_char[command_index_end] = 0;
}

void handleCommand()
{
  // Check if forward is activated
  if (checkBool(&bool_holder_1, BOOL_FORWARD))
  {
    // deactivate
    clearBool(&bool_holder_1, (uint8_t)BOOL_FORWARD);
    setBool(&bool_holder_1, (uint8_t)BOOL_FORWARD_ACTIVE);
    // run for X amount of seconds

  //Serial.println("Forward activated!");

    forward_timer = millis(); // Set timer to deactivate
  }

  // Run timer to deactivate
  if (((millis() - forward_timer) >= (long)FORWARD_TIME) && checkBool(&bool_holder_1, BOOL_FORWARD_ACTIVE))
  {
  //Serial.println("Forward deactivated!");
    clearBool(&bool_holder_1, BOOL_FORWARD_ACTIVE);
  }

  if (checkBool(&bool_holder_1, BOOL_REVERSE))
  {
    // deactivate
    clearBool(&bool_holder_1, (uint8_t)BOOL_REVERSE);
    setBool(&bool_holder_1, (uint8_t)BOOL_REVERSE_ACTIVE);
    // run for X amount of seconds

  //Serial.println("Reverse activated!");
    reverse_timer = millis(); // Set timer to deactivate
  }

  // Run timer to deactivate
  if (((millis() - reverse_timer) >= (long)REVERSE_TIME) && checkBool(&bool_holder_1, BOOL_REVERSE_ACTIVE))
  {
  //Serial.println("Reverse deactivated!");
    clearBool(&bool_holder_1, BOOL_REVERSE_ACTIVE);
  }

  if (checkBool(&bool_holder_1, BOOL_LEFT))
  {
    // deactivate
    clearBool(&bool_holder_1, (uint8_t)BOOL_LEFT);
    setBool(&bool_holder_1, (uint8_t)BOOL_LEFT_ACTIVE);
    // run for X amount of seconds
  //Serial.println("Left activated!");
    left_timer = millis(); // Set timer to deactivate
  }

  // Run timer to deactivate
  if (((millis() - left_timer) >= (long)LEFT_TIME) && checkBool(&bool_holder_1, (uint8_t)BOOL_LEFT_ACTIVE))
  {
  //Serial.println("Left deactivated!");
    clearBool(&bool_holder_1, BOOL_LEFT_ACTIVE);
  }

  if (checkBool(&bool_holder_1, (uint8_t)BOOL_RIGHT))
  {
    // deactivate
    clearBool(&bool_holder_1, (uint8_t)BOOL_RIGHT);
    setBool(&bool_holder_1, (uint8_t)BOOL_RIGHT_ACTIVE);
    // run for X amount of seconds

  //Serial.println("Right activated!");
    right_timer = millis(); // Set timer to deactivate
  }

  // Run timer to deactivate
  if (((millis() - right_timer) >= (long)RIGHT_TIME) && checkBool(&bool_holder_1, (uint8_t)BOOL_RIGHT_ACTIVE))
  {
  //Serial.println("Right deactivated!");
    clearBool(&bool_holder_1, BOOL_RIGHT_ACTIVE);
  }

  if( checkBool(&bool_holder_2, (uint8_t)BOOL_MOWER))
  {
    if(checkBool(&bool_holder_2, (uint8_t)BOOL_MOWER_ACTIVE))
    {
      clearBool(&bool_holder_2, (uint8_t) BOOL_MOWER_ACTIVE);
    //Serial.println("Mower de-activated!");
    }
    else
    {
    //Serial.println("Mower activated!");
      setBool(&bool_holder_2, (uint8_t) BOOL_MOWER_ACTIVE);
    }

    clearBool(&bool_holder_2, (uint8_t) BOOL_MOWER);
  }
}

//bool toggle = false;
void executeCommand()
{
  // if(toggle){
  // // MotorControl.motorForward(0, 255);
  // // MotorControl.motorForward(1, 255);
  // digitalWrite(MOTOR_TRACK_1_1, HIGH);
  // digitalWrite(MOTOR_TRACK_1_2, LOW);
  // toggle = false;
  // delay(1000);
  // }
  // else{
  //   // MotorControl.motorReverse(0, 255);
  //   // MotorControl.motorReverse(1, 255);

  // digitalWrite(MOTOR_TRACK_1_2, HIGH);
  // digitalWrite(MOTOR_TRACK_1_1, LOW);
  // toggle= true;
  //   delay(1000);
  // }
  // Serial.println(toggle);

  if (checkBool(&bool_holder_1, BOOL_FORWARD_ACTIVE)){
    MotorControl.motorForward(0, 255);
    MotorControl.motorForward(1, 255);
  }

  if (checkBool(&bool_holder_1, BOOL_REVERSE_ACTIVE)){
    MotorControl.motorReverse(0, 255);
    MotorControl.motorReverse(1, 255);
  }

  if (checkBool(&bool_holder_1, BOOL_LEFT_ACTIVE)){
    MotorControl.motorForward(0, 255);
    MotorControl.motorReverse(1, 255);
  }

  if (checkBool(&bool_holder_1, BOOL_RIGHT_ACTIVE)){
    MotorControl.motorReverse(0, 255);
    MotorControl.motorForward(1, 255);
  }

  if (
    checkBool(&bool_holder_1, BOOL_FORWARD_ACTIVE) == 0 && 
    checkBool(&bool_holder_1, BOOL_REVERSE_ACTIVE) == 0 && 
    checkBool(&bool_holder_1, BOOL_LEFT_ACTIVE)  == 0 && 
    checkBool(&bool_holder_1, BOOL_RIGHT_ACTIVE) == 0 )
    {
      MotorControl.motorsStop();
    }

  if (checkBool(&bool_holder_2, BOOL_MOWER_ACTIVE))
  {
    if((millis()-ramp_timer) > MOWER_RAMP_TIME && (!checkBool(&bool_holder_2, BOOL_MOWER_RAMP_DONE) || (mower_value != 0)))
    {
      ramp_timer = millis();     

      if(mower_value == MOWER_MAX_VALUE)
      {
        setBool(&bool_holder_2, BOOL_MOWER_RAMP_DONE);
      }
      else
      {
        mower_value++;
      }
      analogWrite(MOTOR_MOWER_EN, mower_value);
      
    }

    // analogWrite(MOTOR_MOWER_EN, MOWER_MAX_VALUE);
  }
  else
  {
    if((millis()-ramp_timer) > MOWER_FALL_TIME && (checkBool(&bool_holder_2, BOOL_MOWER_RAMP_DONE) || (mower_value != MOWER_MAX_VALUE) ))
    {
      ramp_timer = millis();     

      if(mower_value == 0)
      {
        clearBool(&bool_holder_2, BOOL_MOWER_RAMP_DONE);
      }
      else
      {
        mower_value--;
      }
      analogWrite(MOTOR_MOWER_EN, mower_value);
      
    }

    // analogWrite(MOTOR_MOWER_EN, 0);
  }
}

void setBool(uint8_t *bool_carrier, uint8_t bool_place)
{
  *bool_carrier |= 0b1 << bool_place;
}

void clearBool(uint8_t *bool_carrier, uint8_t bool_place)
{
  *bool_carrier &= ~(0b1 << bool_place);
}

uint8_t checkBool(uint8_t *bool_carrier, uint8_t bool_place)
{
  return *bool_carrier & (0b1 << bool_place);
}

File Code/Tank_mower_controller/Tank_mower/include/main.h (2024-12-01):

#ifndef MAIN_H
#define MAIN_H

#include <stdbool.h>
#include <stdint.h>

//Define pinouts
#define IO_EXTENDER_INTERUPT 17

#define SS 5
#define SCK 18
#define MISO 19
#define MOSI 23

#define VCC_MOTOR_TRACK_EN 13
//#define VCC_MOTOR_MOWER_EN 35  //Not working
// #define VCC_MOTOR_TRACK_EN 33
// #define VCC_MOTOR_MOWER_EN 36

//#define ENCODER_1 33
//#define ENCODER_2 36

#define BATTERY_VOLTAGE_SCALED 35//12
#define MOTOR_CURRENT_MOWER 32
#define MOTOR_TRACK_1_CURRENT 34
#define MOTOR_TRACK_2_CURRENT 39

#define MOTOR_TRACK_1_1 25
#define MOTOR_TRACK_1_2 26

#define MOTOR_TRACK_2_1 27
#define MOTOR_TRACK_2_2 14
#define MOTOR_MOWER_EN 4
#define MOTOR_TRACK_1_FAULT P5
#define MOTOR_TRACK_2_FAULT P4
#define MOTOR_TRACK_1_EN P7
#define MOTOR_TRACK_2_EN P6

#define LED_1 P3
#define LED_2 P2
#define LED_3 P1
#define LED_4 P0

void readCommand();
void calculateCurrent(uint8_t pin, float* current);
void calculateVoltage(uint8_t pin, float* voltage);
void displayData();
void handleCommand();
void executeCommand();
void setBool(uint8_t *bool_carrier, uint8_t bool_place);

void clearBool(uint8_t *bool_carrier, uint8_t bool_place);

uint8_t checkBool(uint8_t *bool_carrier, uint8_t bool_place);

#endif

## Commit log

2024-12-01 Add all content
    [3-6V_DC-Toy-Motor.step, 3587.PcbLib, 3587.SchLib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]
2024-12-01 Add docs folder
    [Calculations.ods]
2024-12-13 Update files
    [Calculations.ods]
2024-12-17 Cleanup + add content to readme
    [Battery_holder.stl, Blade.stl, Chassy_body.stl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]
